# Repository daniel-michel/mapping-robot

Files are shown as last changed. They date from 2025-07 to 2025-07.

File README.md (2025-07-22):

# Mapping Robot

This repository contains the code for a mapping robot.
Most functionality is written in TypeScript, including a simulation.
There is also a C++ program for an Arduino, which enables the TypeScript program to use an actual robot by connecting over USB-Serial.

The main TypeScript program is located in the `src` directory.
The C++ Arduino program can be found in the `arduino/robot` directory.

You can try out the TypeScript program at https://daniel-michel.github.io/mapping-robot/.

## Running the Program

The TypeScript program can either be accessed at https://daniel-michel.github.io/mapping-robot/ or run locally by cloning the repository, running `npm run dev` in the root directory, and opening the shown URL in your browser.

To use the physical robot, you first need to set up the hardware as described below (including uploading the Arduino program).
Then you can connect the Arduino over USB.
Now you can use the TypeScript program and click on `Use Physical Robot` and `Connect Robot` to establish a connection. Make sure to use a [browser that supports the Web Serial API](https://caniuse.com/web-serial).

> If, for some reason, when clicking `Connect Robot` no devices are found, you might want to try removing the filters at [arduino-robot.ts:124](./src/logic/robot/arduino-robot.ts#L124-L129)

## Robot Hardware

| Part | Quantity |
| --- | --- |
| Arduino Nano | 1 |
| Stepper Motor | 2 |
| Servo Motor | 1 |
| Range Sensor | 1 |
| 3D-Printed body | 1 |
| 3D-Printed wheels | 2 |
| 3D-Printed ball wheel | 1 |
| 3D-Printed sensor mount | 1 |

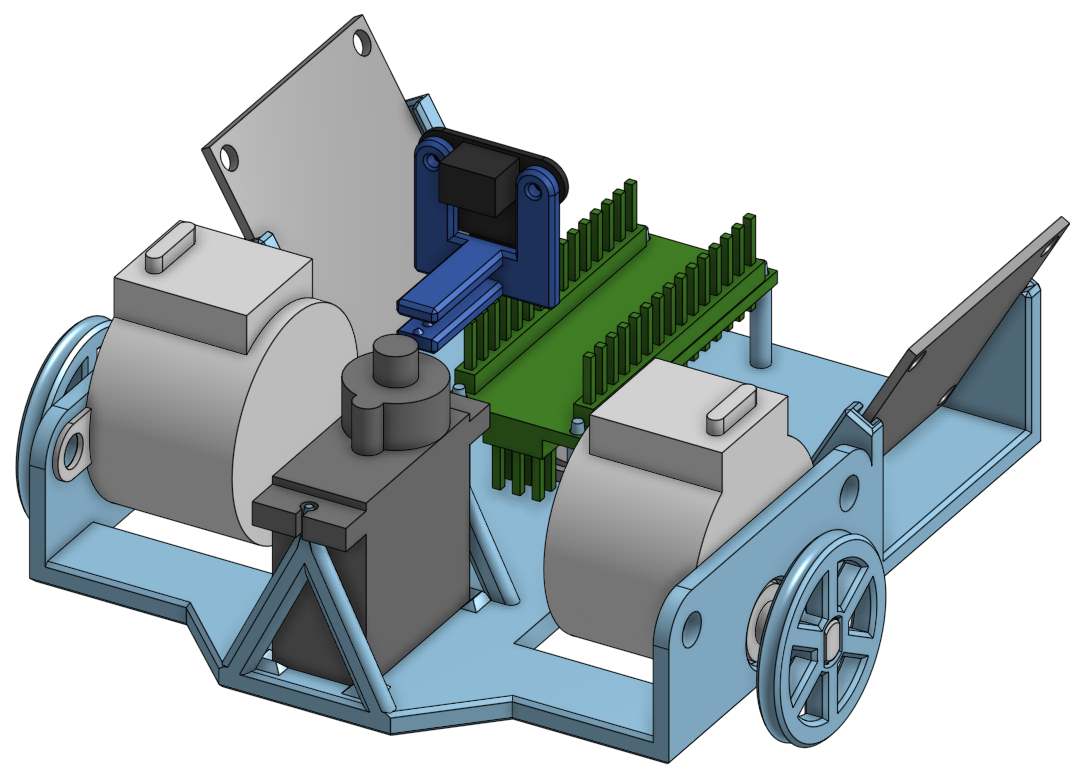
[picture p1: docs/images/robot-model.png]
Model of the assembled parts


### Arduino Nano

An Arduino Nano is used for controlling the robot's motors and reading the sensor.
The program in [`arduino/robot`](./arduino/robot/) is used for communicating with the TypeScript program and receives commands to control the motors or read sensor data.

### Stepper Motors

28BYJ-48 stepper motors with ULN2003 driver boards

| Right Driver Board | Arduino Nano |
| --- | --- |
| IN1 | D4 |
| IN2 | D5 |
| IN3 | D6 |
| IN4 | D7 |

| Left Driver Board | Arduino Nano |
| --- | --- |
| IN1 | D9 |
| IN2 | D10 |
| IN3 | D11 |
| IN4 | D12 |

Power should be provided by an external 5V power supply.

### Servo Motor

Tower Pro MG90S servo motor

The positioning was not very accurate, therefore the need for the calibration values in [motors.h:36](./arduino/robot/motors.h#L36-L39).

| Servo  | Arduino Nano |
| --- | --- |
| Signal | D2 |

Power should be provided by an external 5V power supply.

### Range Sensor

Waveshare TOF Laser Range Sensor Mini

| TOF Sensor | Arduino Nano |
| --- | --- |
| VCC | 5V |
| GND | GND |
| SDA | A4 |
| SCL | A5 |

The sensor is used in IIC mode in this project.

#### Configuration

There are scripts on the [Waveshare Wiki](https://www.waveshare.com/wiki/TOF_Laser_Range_Sensor_Mini) that might be useful for testing the sensor in the configured mode. Note that the wiring diagrams on the Wiki are not completely consistent.

There are two Python scripts for configuring the mode (UART, IIC) using a Raspberry Pi.
The IIC mode is used for this project, but the default mode is UART.
If the mode has not already been changed to IIC, it can be changed using these scripts.

##### Reset to UART mode

Initially, the sensor should be in UART mode. Otherwise, to reset it to UART mode, the [reset_sensor.py](./rasp_sensor_scripts/reset_sensor.py) script can be used.
For this, the instructions in [the FAQ section of the Waveshare Wiki](https://www.waveshare.com/wiki/TOF_Laser_Range_Sensor_Mini#FAQ) can be adjusted to:

1. Connect the sensor for UART communication. Connect the TX, RX, and GND wires of the Raspberry Pi to the corresponding pins of the TOF module, temporarily disconnect the VCC pin, and start the Raspberry Pi.
2. Start the [reset_sensor.py](./rasp_sensor_scripts/reset_sensor.py) script on the Raspberry Pi.
3. At this point, connect the 5V of the Raspberry Pi to the VCC pin of the TOF module. The module will switch to UART mode and start outputting data. Use CTRL+C to stop the program, then unplug the TOF module.

##### Configure IIC mode

1. To configure the sensor for IIC mode, first make sure it is in UART mode.
2. Connect the TOF module in the UART configuration with the Raspberry Pi.
3. Run [change_sensor_to_iic.py](./rasp_sensor_scripts/change_sensor_to_iic.py).
   The sensor should then be configured in IIC mode.

### 3D-Printed Parts

The parts did not fit perfectly for me and probably need adjustments.

The original parts can be found on [Onshape](https://cad.onshape.com/documents/9786b54982b96f282970ed90/w/a34a31064c99de7c25494cb7/e/251084b2ad647410587588c3).
There is also an STL file of the parts: [All Robot Parts.stl](./robot-3d-print/All%20Robot%20Parts.stl).

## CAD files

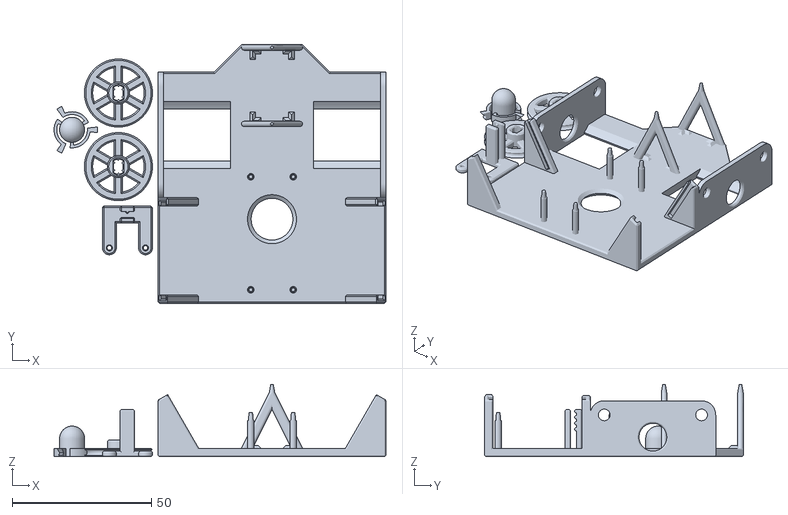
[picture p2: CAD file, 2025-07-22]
robot-3d-print/All Robot Parts.stl
119.4 x 93.0 x 26.0

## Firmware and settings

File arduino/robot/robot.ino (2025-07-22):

#include "TOF_Reader.h"
#include "motors.h"
#include "helper.h"

const int ledPin = 13;  // the number of the bulit-in LED pin
int count = 0;

void read_serial_input();
void print_TOF_to_serial(TOF_Parameter tof);

void setup() {
  Serial.begin(9600);
  pinMode(ledPin, OUTPUT);
  init_motors();

  Wire.begin();  //Initialize Hardware I2C 初始化硬件I2C
  Wire.setClock(400000);

  test_sequence();
}

void test_sequence() {
  delay(500);
  set_sensor_direction(-1);
  set_sensor_direction(1);
  set_sensor_direction(0);
  // delay(1000);
  // scan(0, 100);
  // drive_command(0, 500, 1000);
  // drive_command(1, 1000, 500);
  // drive_command(1, -1000, -500);
  // drive_command(1, -500, -1000);
  // set_sensor_direction(0);
  // set_sensor_direction(-1);
  // set_sensor_direction(1);
  // set_sensor_direction(0);
}

void loop() {
  // Serial.print("log:loop ");
  // Serial.println(count, DEC);

  // int read = Serial.read();
  // if (read >= 0) {
  //   Serial.print("log:read ");
  //   Serial.println((char)read);
  // }

  // TOF_Active_Decoding();
  // TOF_Parameter data = Get_TOF();
  // print_TOF_to_serial(data);

  read_serial_input();

  count++;
  delay(200);
}

const byte msg_start[] = { 0, 13, 10 };
int start_index = 0;

void read_serial_input() {
  if (!Serial.available()) {
    return;
  }
  while (Serial.available() && start_index < 3) {
    int data = Serial.read();
    if (data != msg_start[start_index]) {
      start_index = 0;
    }
    if (data == msg_start[start_index]) {
      start_index++;
    }
  }

  if (!Serial.available()) {
    return;
  }

  if (start_index == 3) {
    start_index = 0;

    // read message
    int length = Serial.read();
    if (length < 3) {
      Serial.println("log did not receive message");
      return;
    }
    byte* data = malloc(length);
    int received_length = Serial.readBytes(data, length);
    if (received_length == length) {
      // received complete message
      // Serial.print("log received");
      // for (int i = 0; i < length; i++) {
      //   Serial.print(" ");
      //   Serial.print(data[i], HEX);
      // }
      // Serial.println();

      uint16_t id = read_uint16(data, 0);
      int command = data[2];
      Serial.print("log id ");
      Serial.print(id, DEC);
      Serial.print(" command ");
      Serial.print(command, DEC);
      Serial.println();

      if (command == 1) {
        // drive
        if (length < 5) {
          return;
        }
        int left_steps = read_int16(data, 4);
        int right_steps = read_int16(data, 6);
        drive_command(id, left_steps, right_steps);
      } else if (command == 5) {
        // scan
        int count = data[3];
        scan(id, count);
      } else {
        // unknown
        Serial.print("err unknown command ");
        Serial.println(command, DEC);
      }

      Serial.print("data ");
      Serial.print(id, DEC);
      Serial.println(":$");
    }
    delete data;
  }
}

void drive_command(uint16_t id, int left_steps, int right_steps) {
  float ratio = (float)abs(left_steps) / (float)(abs(left_steps) + abs(right_steps));

  int max_steps_at_once = 10;

  while (left_steps != 0 || right_steps != 0) {
    if (left_steps == 0) {
      rotate_right(right_steps);
      break;
    }
    if (right_steps == 0) {
      rotate_left(left_steps);
      break;
    }
    float curr_ratio = (float)abs(left_steps) / (float)(abs(left_steps) + abs(right_steps));
    if (curr_ratio > ratio) {
      // move left
      int count = min(abs(left_steps), max_steps_at_once);
      int step = sign(left_steps) * count;
      rotate_left(step);
      left_steps -= step;
    } else {
      // move right
      int count = min(abs(right_steps), max_steps_at_once);
      int step = sign(right_steps) * count;
      rotate_right(step);
      right_steps -= step;
    }
  }
}

void scan(uint16_t id, uint16_t count) {
  for (int i = 0; i < count; i++) {
    float direction = -((float)i / (float)(count - 1)) * 2.0 + 1.0;
    set_sensor_direction(direction);
    TOF_Parameter data = Get_TOF();
    Serial.print("data ");
    Serial.print(id, DEC);
    Serial.print(":");
    Serial.print(i, DEC);
    Serial.print(",");
    Serial.print(data.dis_status, DEC);
    Serial.print(",");
    Serial.print(data.dis, DEC);
    Serial.println();
  }
  set_sensor_direction(0);
}

void print_TOF_to_serial(TOF_Parameter tof) {
  Serial.print("tof:");
  Serial.print(tof.id, DEC);
  Serial.print(",");
  Serial.print(tof.dis_status, DEC);
  Serial.print(",");
  Serial.print(tof.dis, DEC);
  Serial.print(",");
  Serial.print(tof.signal_strength, DEC);
  Serial.print(",");
  Serial.print(tof.system_time, DEC);
  Serial.print(",");
  Serial.println(tof.range_precision, DEC);
}

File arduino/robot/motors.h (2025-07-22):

#pragma once
#include "Arduino.h"
#include "helper.h"
#include <Stepper.h>
#include <Servo.h>

void set_sensor_direction(float direction);

const int stepsPerRevolution = 2048;
const int stepper_speed = 10;
const int servo_pint = 2;
// rpm = (steps / steps-per-rotation) / time(min)
// time(min) = (steps / steps-per-rotation) / rpm
const float time_per_step_ms = 60.0 * 1000.0 / (float)stepsPerRevolution / (float)stepper_speed;

Stepper left_motor = Stepper(stepsPerRevolution, 9, 11, 10, 12);
Stepper right_motor = Stepper(stepsPerRevolution, 4, 6, 5, 7);
Servo sensor_servo;
float current_servo_position = 0.0;

void init_motors() {
  left_motor.setSpeed(stepper_speed);
  right_motor.setSpeed(stepper_speed);
  sensor_servo.attach(2);

  set_sensor_direction(0);
}

// direction is expected to be a value between -1 and 1
void set_sensor_direction(float direction) {
  if (direction > 1 || direction < -1) {
    Serial.println("err Sensor direction out of range");
    return;
  }

  // calibration values for the specific servo motor
  float left_most = 0.3;
  float center = -0.25;
  float right_most = -0.9;

  float adjusted_value = direction < 0.0 ? map(direction, -1, 0, left_most, center)
                                         : map(direction, 0, 1, center, right_most);

  int microseconds = (adjusted_value + 2) * 1000;

  float dir_diff = abs(direction - current_servo_position);

  sensor_servo.writeMicroseconds(microseconds);
  float speed = 60.0 / 170.0; // it takes 170 milliseconds to rotate 60 degrees (in the spec sheet it is 100 milleseconds for 60 degrees)
  delay((int)((dir_diff / 2 * 135) / speed) + 100); // add 100 milliseconds to ensure it has stopped
  current_servo_position = direction;
}

void rotate_left(int steps) {
  left_motor.step(steps);
}

void rotate_right(int steps) {
  right_motor.step(-steps);
}

void rotate_both(int left, int right) {
  left_motor.step(left);
  right_motor.step(-right);
}

// void rotate_motors(int steps_left, int steps_right) {
//   float ratio = (float)abs(steps_left) / (float)(abs(steps_left) + abs(steps_right));
//   while (steps_left != 0 || steps_right != 0) {
//     if (steps_left == 0) {
//       rotate_right(steps_right);
//       return;
//     }
//     if (steps_right == 0) {
//       rotate_left(steps_left);
//       return;
//     }
//     float curr_ratio = (float)abs(steps_left) / (float)(abs(steps_left) + abs(steps_right));
//     if (curr_ratio > ratio) {
//       // move left
//       int step = sign(steps_left);
//       rotate_left(step);
//       steps_left -= step;
//     } else {
//       // move right
//       int step = sign(steps_right);
//       rotate_right(step);
//       steps_right -= step;
//     }
//   }
// }

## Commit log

2025-07-22 add arduino code
2025-07-22 add readme and 3d models
    [All Robot Parts.stl]
